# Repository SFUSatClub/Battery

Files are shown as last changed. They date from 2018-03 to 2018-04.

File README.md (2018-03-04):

# Battery Board
KiCad project for the cubesat battery board. This board holds 2 18650 cells in series with protection circuitry. This board follows PC104 dimentions.

This repository uses the SFU Satellite Team's KiCad component library as a submodule.
To start working on the repository:

```
1. Open a git shell
2. Navigate to the directory you wish to place the repository inside
3. git clone --recursive "https://github.com/SFUSatClub/Battery.git"
```

If you modify either the component schematic or footprint libraries you must push those changes to the SFUSatClub/KiCad-Lib repository, then commit the project repository.

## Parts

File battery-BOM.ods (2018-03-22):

reference | name | Digikey PN | Quantity
J6 | B3B-XH-A(LF)(SN) | 455-2248-ND | 3
J6,J11,J12 | B3B-XH-A(LF)(SN) mating |  | 1
U1 | BQ29209 | 296-27677-1-ND | 1
BT1,BT2 | Battery_Cell | 36-1042-ND | 2
R5,R6 | 100R | 311-100HRTR-ND | 2
C1,C2,C4 | 0.1uF | 490-1524-1-ND | 3
R4 | 250R | RNCF0603TKY250RCT-ND | 1
R3 | 160R | 311-160GRCT-ND | 1
C3 | 0.33uF | 445-5684-1-ND | 1
R2 | 1k | P1.0KDECT-ND | 1

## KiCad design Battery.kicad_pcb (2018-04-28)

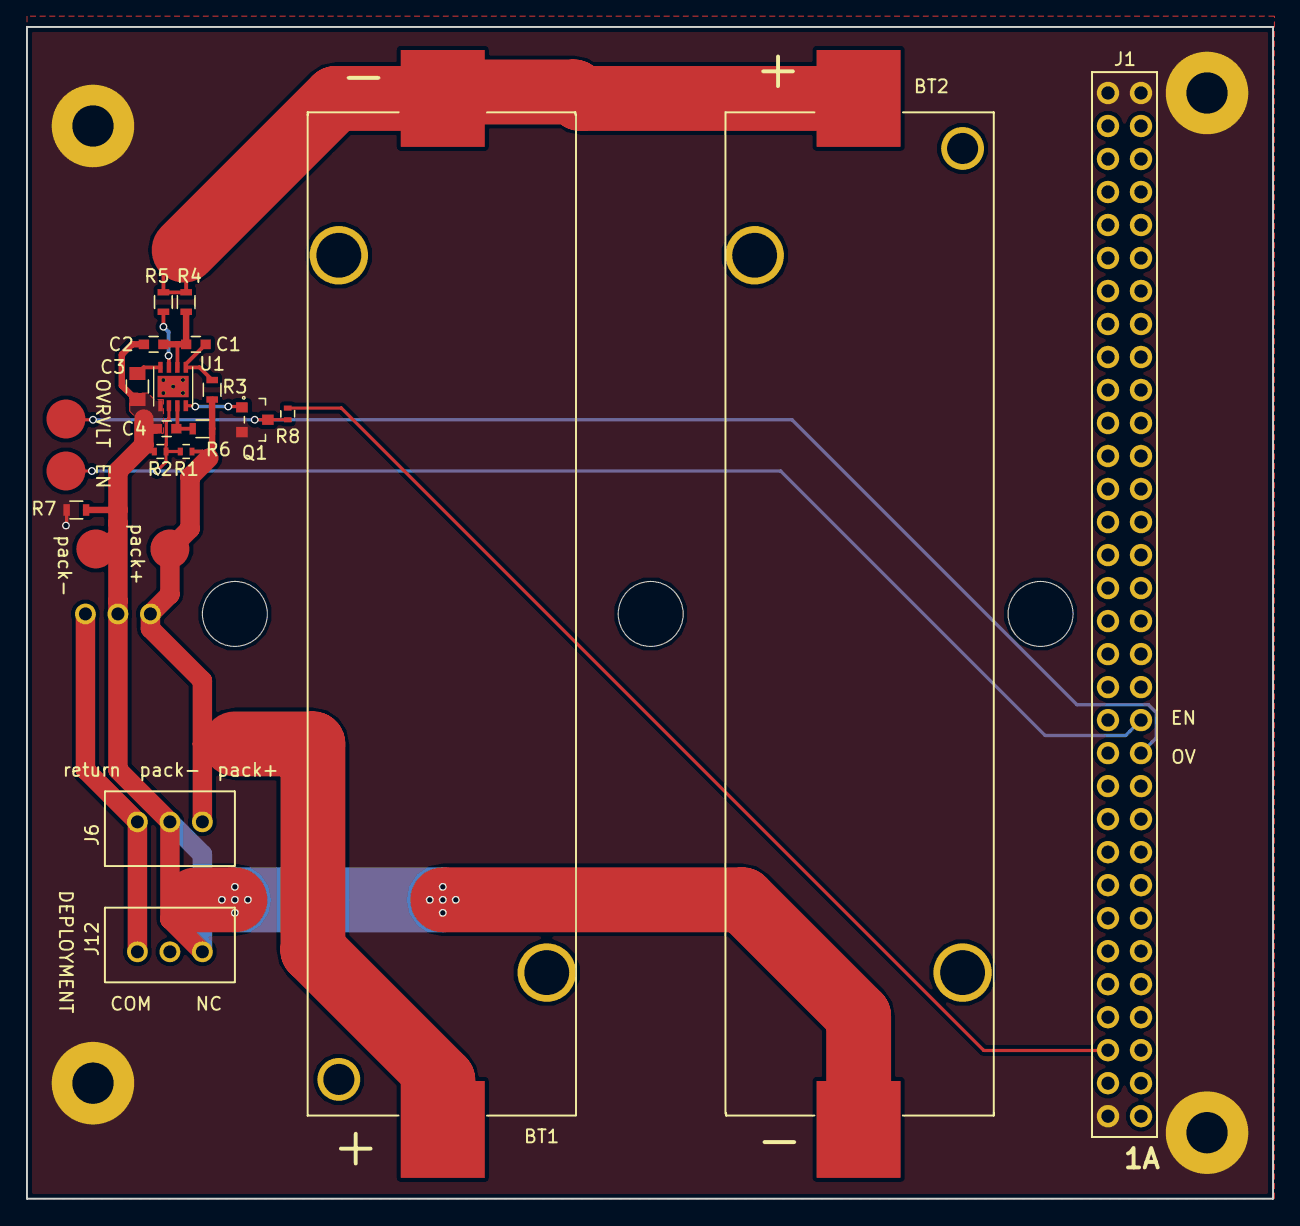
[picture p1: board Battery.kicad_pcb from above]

Board: 2 copper layers, 95.9 x 90.2 mm, 28 parts (1 on the bottom side), 14 nets.

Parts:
BT1, BT2: Battery_Cell; 1042-BattHolder
C1, C2, C4: 0.1uF; C_0603
C3: 0.33uF; C_0805
J1: PC104-8BIT; PC104-8bit
J2, J3, J4, J5: PC104PTH
J6, J11, J12: B3B-XH-A(LF)(SN); B3B-XH-A
J7, J8, J9, J10: TEST_1P; Measurement_Point_Round-SMD-Pad_Big
Q1: 2N7002ET1G; SOT-23-3
R1: DNP; R_0402
R2: 1k; R_0402
R3: 160R; R_0603
R4: 250R; R_0603
R5, R6: 100R; R_0603
R7: DNP; R_0603
R8: R_10k0_1%_0.063W_0402; R_0402
U1: BQ29209; VDFN-8

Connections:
+3V3: J1.3B, R8.1
/OVR_VLT: J1.12A, J8.1, Q1.3, R8.2
/SeriesBatteryCell/PACK+: BT1.1, J6.1, J9.1, J11.3, R1.1, R3.1, R6.1
/SeriesBatteryCell/PACK-: BT2.2, C2.2, C3.2, C4.2, J6.2, J10.1, J11.2, J12.3, R2.2, R7.1, U1.5
/~CB_EN: J1.13A, J7.1, R1.2, R2.1, U1.6
GND: J1.1B, J1.32A, J1.32B, J2.1, J3.1, J4.1, J5.1, Q1.2, R7.2
unnamed: BT1.2, BT2.1, R4.1, R5.1
unnamed: C1.1, R3.2, U1.1
unnamed: C1.2, C2.1, R4.2, U1.2
unnamed: C3.1, U1.4
unnamed: C4.1, R6.2, U1.7
unnamed: J6.3, J11.1, J12.1
unnamed: R5.2, U1.3
OUT: Q1.1, U1.8

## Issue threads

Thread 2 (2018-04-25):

Overvoltage and balance enable test points mislabeled

TobiNakamura, 2018-04-25:
The silkscreen labels for the test points are reversed.

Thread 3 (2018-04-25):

Overvoltage detect signal level shifting

TobiNakamura, 2018-04-25:
Overvoltage detect output is 5.9V nominal. Needs to be shifted to 3.3V for the OBC. This level shifting should be done on the battery board for logical clarity.

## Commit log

2018-03-05 balancing enabled by default using 1k PD. Can override by pulling line high from OBC
    [Battery.kicad_pcb, Battery.sch, SeriesBatteryCell.sch]
2018-03-15 layout complete
    [Battery.kicad_pcb, Battery.sch, SeriesBatteryCell.sch]
2018-03-22 moved bottom side DC connector to avoid the RFB pin path on the eps board
    [Battery.kicad_pcb, battery-BOM.ods]
2018-03-22 generated gerbers
    [Battery-B.Cu.gbr, Battery-B.Mask.gbr, Battery-B.SilkS.gbr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]
2018-04-28 Revision 2. Fixed silkscreen labelling issue with EN/OVR_VLT test points, Added level shifter for OVR_VLT output as IC outputs more than 3.3V
    [Battery.kicad_pcb, Battery.sch, SeriesBatteryCell.sch]
2018-04-29 added soldermask width requirement to fab notes
